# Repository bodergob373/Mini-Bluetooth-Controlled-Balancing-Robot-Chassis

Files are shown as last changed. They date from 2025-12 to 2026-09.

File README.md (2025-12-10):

# Mini Bluetooth-Controlled Balancing Robot Chassis

## Description
A small chassis for a wheeled balancing robot. Its two Nidec 24H motors have built-in encoders and are powered by a thin 2200mAh LiPo. The GY-BNO055 IMU provides the ESP32 with orientation feedback for balancing. It can be controlled by Bluetooth commands.

## Why?
I tried building a balancing robot in the past for a hardware hackathon. It used NEMA17 stepper motors. It sucked and probably wouldn't have ever worked. That's why I want to make one that uses BLDC motors and actually works.

## The Model





## Wiring Diagram


## BOM:
Links here: https://docs.google.com/spreadsheets/d/15BZOgCAK9HfxFjphhOrtfexejHQh9IfhAeZVUUb6IY0/edit?usp=sharing

| Item | Purpose | Item Type | Order Amount | Cost |
|---|---|---|---|---|
| jumpers | Wiring components | 3 kinds 10cm | 1 | $3.16 |
| gy-bno055 | Sensing orientation | N/A | 1 | $13.18 |
| lm2596 | Powering the ESP32 | 1 PCS | 1 | $1.71 |
| nidec 24h055mo20 | Driving the wheels | N/A | 2 | $17.54 |
| esp32 devboard | Controlling the robot | ESP32 Type-C 30Pin | 1 | $4.17 |
| 10x15x4 mm bearing | Low-friction wheel hubs | 10x15X4mm | 1 | $2.85 |
| m2.5x8 screws | Securing the motors | M2.5 50PCS, x8mm | 1 | $2.20 |
| m3x5 tapping screws | Mounting the LM2596 | M3 x 50Pieces, 5mm | 1 | $1.50 |
| m3x8 tapping screws | Mounting the drive modules and ESP32 | M3x8mm, 20pcs | 1 | $1.40 |
| silicone bands | High-friction tires | Any | 1 | $7.99 |
| 3S LiPo | Powering the robot | 1Pcs | 1 | $19.89 |
| 10uF ceramic capacitor | Protect ESP32 from current spikes | N/A | 1 | $0 |
| 220uF electrolyitc capacitor | Protect ESP32 from current spikes | N/A | 1 | $0 |

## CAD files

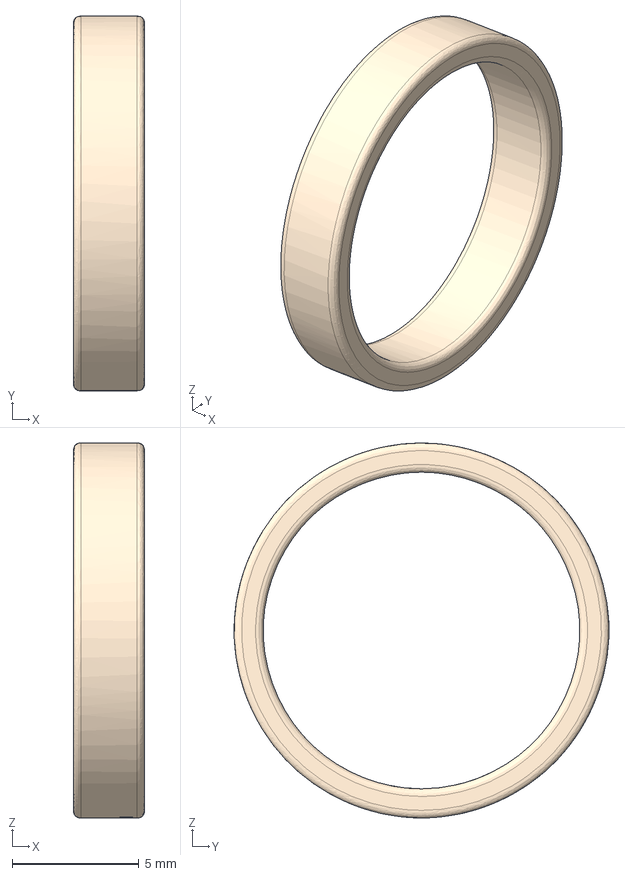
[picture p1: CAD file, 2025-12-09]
CAD/printable_parts/bearing_spacer.step
2.80 x 14.8 x 14.8 mm

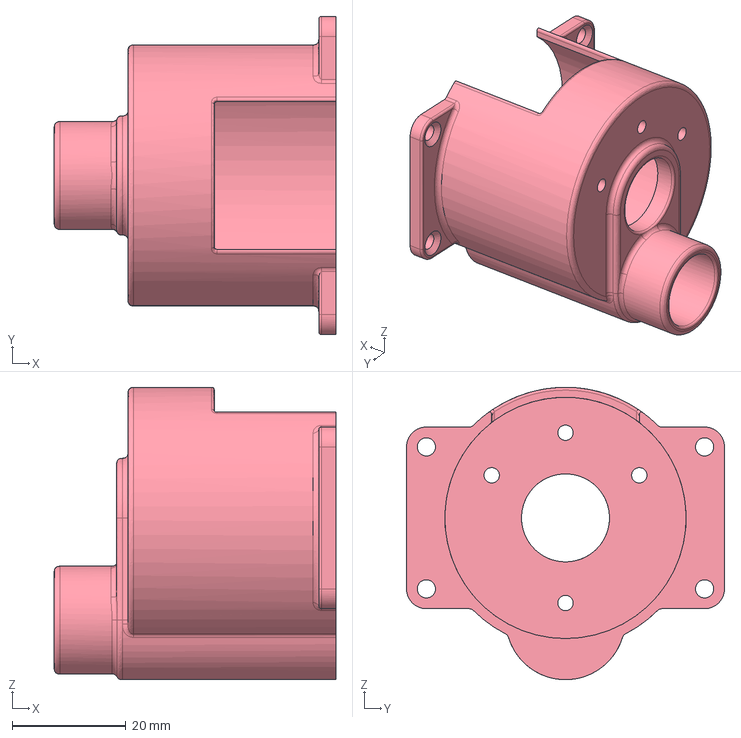
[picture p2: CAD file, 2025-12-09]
CAD/printable_parts/motor_case.step
49.6 x 56.0 x 51.5 mm

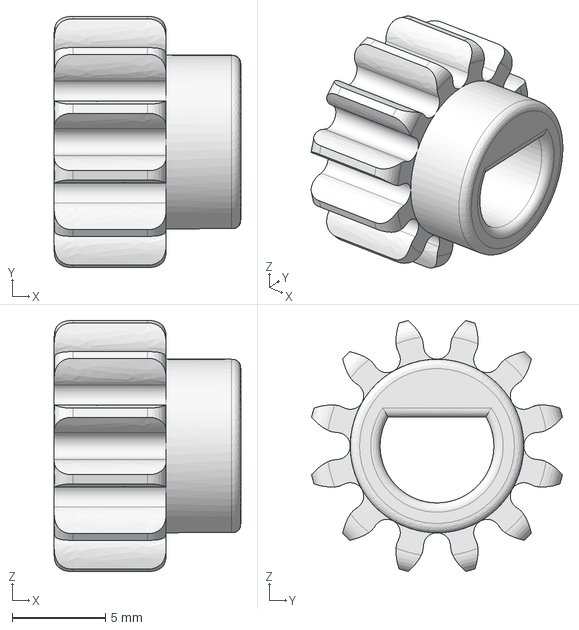
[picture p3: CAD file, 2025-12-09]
CAD/printable_parts/spur_gear.step
10.0 x 13.5 x 13.5 mm

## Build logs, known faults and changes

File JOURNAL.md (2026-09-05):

---
Title: Mini Bluetooth-Controlled Balancing Robot Chassis
Author: Jonathan Itoh
Created On: 2025/12/06
Total Time: 21h
---

# 2025/12/2: Research and Choosing Components: 3h
I originally planned for the robot to use brushless RC aircraft motors with planetary gearboxes that spin the wheels through pulleys. I started looking for cheap motors and found A2212 motors. For encoders, I found a magnetic encoder that can be mounted near a small magnet attached to the motor shaft. However, after some checking, I realized that finding cheap, precise ESCs that can handle enough current would be difficult and the whole gearbox + pulleys would create a lot of slop in the wheels, so I scrapped the whole idea. After seeing the motors in videos of balancing reaction wheel cubes, I found out about Nidec 24H BLDC motors, which already have built-in optical encoders and ESCs. They have less power, so I will need to downsize the robot. Even though they have lower RPM, I will still need some sort of gearbox. I decided on putting inverted ring gears inside the wheels that mesh with the spur gears on the motors for decent reduction. For batteries and the microcontroller, I decided to use some sort of ESP32 and 3S LiPo.

Nidec 24H055M020 with a D-shaft



# 2025/12/2: CAD 1: 3.5h
I began designing the robot in Onshape starting with the drive system. For the gears, I got a premade configurable planetary gear feature, set the planet number to 1, deleted the sun gear, and set the tooth count so that it would be a 1:4 ratio.



Most of the robot frame will be designed around the shape of the motors, so I found dimensions and designed a simple model and positioned it with the shaft going through the spur gear.



Before I designed the wheel, I needed good-sized ball bearings that are positioned right. It took really long to do this because the gears needed clearance and I need to make sure that the wheel would wiggle as little as possible. I kept switching between small, wide bearings that fit inside the ring gear and large, narrow bearings that go beside it. Both wouldn't fit right, so I decided to use two small, narrow bearings per wheel. This would allow them to go fit on both sides of the spur gear and provide a lot of support for the wheel. I would be able to connect the outside of both bearings to the motor case and press in a plastic shaft connected to the wheel.



# 2025/12/3: CAD 2: 7h
I raised the motor to make the gears larger so that the spur gear could fit on the motor shaft and the bearings would have some more space. Then, I designed the wheel. I added side ridges on the wheel so that wide rubber bands can be stretched around the wheel for enough grip. I also put a hole through the spur gear.




For the motor case, I first made a tube around both bearings. To prevent the outer bearing from getting pushed in too far, I put a spacer between.



Then, I made a thin case that fits around the entire motor and put holes through for the screws. I didn't want the bearing mount to be floppy, so I made the motor case thicker there. The motor also has a big chunk that sticks out the side for the plug, so I cut that out of the case too. So that the motors can be put into the case, the back would have to be open and the entire wheel + case could be screwed onto the robot base. I added a mounting plate for that and put fillets everywhere to make everything smooth.



Like the motor case, the robot base would have to be designed around the huge battery. To get near the motor's 12V input, I will need a 3s LiPo. It also needs to be thin otherwise the entire robot is gonna be either super wide or extra tall and have some wasted space between the motors. Finding a cheap battery that meets these requirements and has decent capacity took a while, but I eventually found one.



I made the battery case with mounts for connecting the motor assembly. It's only half of the case because it will be mirrored later.



Next, I needed to add the microcontroller, but I had to choose what ESP32 to use. I originally picked a WEMOS Lolin32, but later decided to use a more generic 30-pin ESP32 devboard with mounting holes.




# 2025/12/4: Finished CAD: 4h
It was difficult to find a good place to mount the ESP. The only usable space on the robot base is on the front and back, so I added protrusions on the back that screws can tap into.



For the accelerometer, I will use a BNO055 breakout module because it has built-in orientation calculation, which will simplify the code and probably be more accurate. Because it has no holes for screws but is pretty flat, I added a gap in the robot base that the board can be wedged into.



I also need a buck converter to supply power to the microcontroller, so I found a cheap LM2596 breakout board that meets the power requirements. It has two holes for screws, so I added four more protrusions on the front that allow it to be mounted either up or down.



The parts are finally done. I mirrored the drive module to the other side and moved the components to the right spots.




# 2025/12/5: Added Tolerances: 2h
To prepare for printing, I added configurable tolerances for the parts so that parts like the bearings can fit in and the gears can mesh well. I did this by creating variable tables and using those values in the sketch dimensions and features. In order to do it well, I had to organize and separate some sketches and features.



# 2025/12/5: Wiring Diagram: 1h
I made the wiring diagram. It went smoothly until I found out that there should be capacitors on the buck converter output to protect the ESP32 from current spikes. I also had to research what pins to use on the GY-BNO055 IMU.
